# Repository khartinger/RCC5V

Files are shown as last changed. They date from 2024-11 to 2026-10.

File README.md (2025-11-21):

<table><tr><td></td><td>
Last modified: 2025-11-21 <br>   
<h1>Controlling model railroad components with DCC, MQTT and manually</h1>
<a href="LIESMICH.md">==> Deutsche Version</a>&nbsp; &nbsp; &nbsp; 
</td></tr></table>   

[Directly to the table of contents of this repository](#x20)   

# Introduction
Switching points is an important part of model railroading. There are many ways to control turnouts, uncouplers, disconnectable tracks and other components. Who doesn't want to be able to do this in different ways?    
The following image shows a part of an RCC control (RCC = Railway-Component-Control) with information display, switching and LED feedback.   
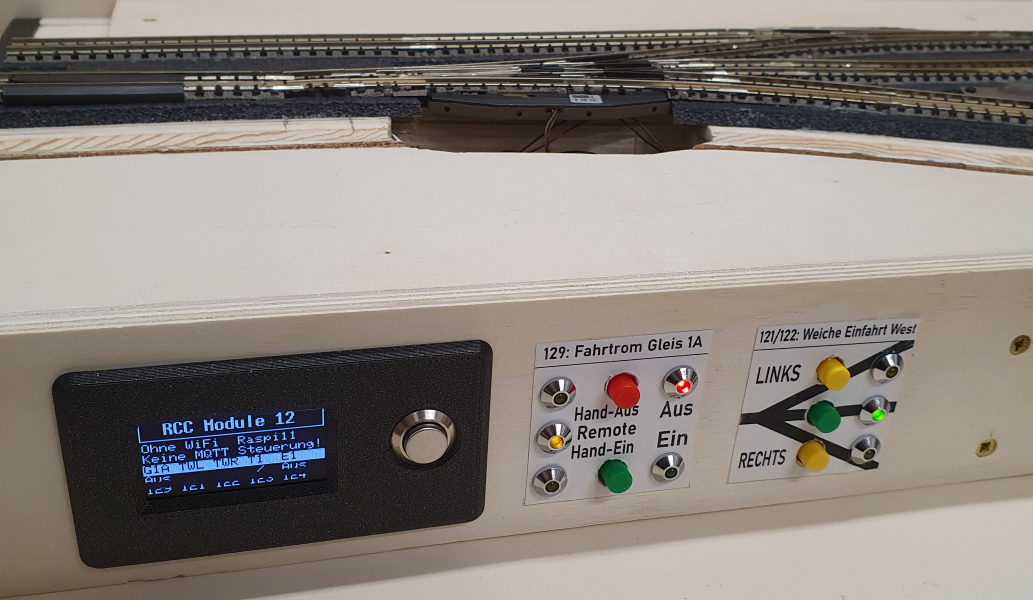
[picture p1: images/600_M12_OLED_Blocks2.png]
Example RCC controller
   
_Figure 1: Example user interface RCC control unit_   

## Traditional switching of turnouts etc.   
The simplest method of switching is, of course, to do it all by hand. In this case, you don't even need point machines. But with more distant or distributed components, this mode of operation quickly becomes cumbersome.   
For this reason, magnetic drives are usually used to switch the components. In the simplest case, the AC voltage is switched directly:   

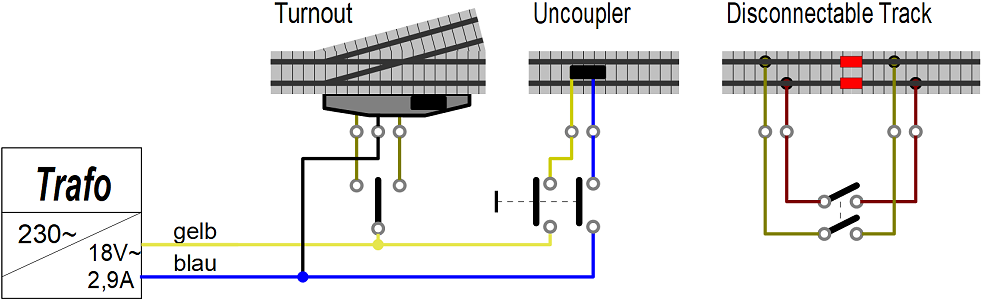
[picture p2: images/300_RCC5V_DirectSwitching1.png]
RCC5V_DirectSwitching
   
_Figure 2: Direct switching of model railway components   
(turnout = turnout, uncoupler = uncoupler track, disconnectable track = disconnectable track)_   

However, direct switching of the AC voltage has disadvantages: There is no feedback on the actual switching status and automatic switching of several components is not possible.   
These disadvantages can be eliminated by commercial, digital control systems. Unfortunately, this is usually associated with considerable costs. For this reason, self-construction is an option, which also offers additional possibilities and flexibility.   

## How to do it better?
If you like building things yourself, you've come to the right place. The low-cost RCC (Railway Component Control) model railroad component controller presented here allows you to switch model railroad components in three different ways:   
* directly on the module or on the layout at the touch of a button   
* via DCC   
* via MQTT commands &uuml;over the WLAN   

In the standard version, up to 32 digital outputs and inputs are available. This means that a maximum of 16 two-way switches or 10 three-way switches etc. can be controlled. This number is normally sufficient for modules.   
Expansion of the system is generally possible and only depends on the I²C-IO expanders used.   

Some skills are advantageous for the successful use of the RCC system:   
* Soldering and some manual dexterity   
* Compiling and uploading a file to an ESP32 microcontroller   
* Basic knowledge of the open source [circuit board layout program KiCad](https://www.kicad.org/)   
* Basic knowledge of MQTT, if MQTT is to be used for control   

# How do I get started?
1. you should first get an overview of the [contents of this repository](#x20) and [the RCC system](#x30). This is provided in the chapters below in this manual.   
2. If the RCC system is the right choice, the requirements for your own system have to be defined:   
* Which components are needed?
* How many of each type are needed?
* Which DCC address for which device?   
_Example demo program_:   
1x uncoupler with DCC address 11, 1x two-way turnout (DCC 21), 1x three-way turnout (DCC 31 and 32), 1x traction current (DCC 41) and 1x flashing light (DCC 51).   
3. the next step is to manufacture the required components. How to do this is described in the chapter [“How do I start the RCC project?” (/fab/rcc0_start/README.md)](/fab/rcc0_start/README.md).   
4. the demo program is then adapted to your own system and the ESP32 microcontroller is programmed. This is described in chapter [`/software/rcc_demo1
/CUSTOMIZE_E.md`](/software/rcc_demo1/CUSTOMIZE_E.md).   
5. Finally, all components are wired and the entire system is tested.   

The detailed description of the [construction of module #12: “passing loop and siding”](/examples/module12/LIESMICH.md) can also be a great help.   

[To the top of the page](#up)   

# Overview
This repository deals with the production and use of components for controlling turnouts, uncouplers, disconnectable tracks etc. on an electric model railroad using DCC, MQTT or manually.   
The following topics are covered in various subdirectories:   

__Information about the system__   
* [How do I begin the RCC project?](/fab/rcc0_start/README.md)   
* [Electrical connection of railroad modules according to NEM 908D](/info/con_NEM908/README.md)   
* [Drill holes and covers for the front of the module](/info/frontpanel/README.md)   

__Manufacturing the system components__   
* [Manufacturing of Components for the power supply](/fab/rcc1_supply/README.md)   
* [Manufacturing of the ESP32-Shields](/fab/rcc2_esp32/README.md)   
* [Manufacturing of i2c boards](/fab/rcc3_i2c/README.md)   
* [Manufacturing of the switching blocks](/fab/rcc4_block/README.md)   
* [Manufacturing of additional boards](/fab/rcc5_add_ons/README.md)   
* [KiCad files of RCC components](/fab/kicad/README.md)   

__Software for the ESP32__   
* [MQTT commands for controlling the components](/software/mqtt/README.md)   
* [Overview of the demo software](/software/rcc_demo1/README.md)   
* [Customize the demo software to your own needs](/software/rcc_demo1/CUSTOMIZE_E.md)   
* [Structure of the demo software in detail](/software/rcc_demo1/DETAILS_E.md)   
* [Automatic execution of MQTT command sequences](/software/mqtt/README.md#x30)   

__Examples, use of the system__   
* [Example wiring of a turnout](/examples/exampleTurnout2/README.md)   
* [Construction of the “RCC block tester”](/examples/blocktester/README.md)   
* [Construction of module 12: “passing loop and siding”](/examples/module12/README.md)   
* [Construction of module 13: “reverse loop - west”](/examples/module13/README.md)   
* [Construction of module 14: “Two tracks to one track”](/examples/module14/README.md)   
* [Conversion of module M01: “Track 1 to 2 with goods shed (2010)”](/examples/module01/README.md)   

__Other practical ideas for modules and the like__   
* [module dust cover](/info/dust_cover/README.md)   

[To the top of the page](#up)   

# The RCC-system at a glance   
The RCC system has a modular structure and mechanically consists of a series of modules or blocks. Logically, it consists of six parts:   

1. __FEED-IN__ (power supply): Generation and provision of the supply voltage (here AC voltage) and the DCC signals for the RCC system by external components.   
2. __SUPPLY__ (module supply): The AC voltage, the traction current and the DCC signal for switching the magnetic articles are taken from the 25-pin plug according to NEM908 and a separate 5V DC voltage is generated.   
3. __&micro;C__ (microcontroller): The microcontroller, equipped with additional shields, is used to control the module. An ESP32 is used, which also handles communication with the MQTT broker.  
4. __I2C__: Connection between the microcontroller and the control blocks (RCC blocks). I2C I/O expander boards with PCF8574 are used for this purpose.   
5. __RCC block__: The control element for _a_ model railroad component with local operating and display elements.   
6. the __model railroad components__ such as turnouts, uncouplers and disconnectable tracks.   

RCC5V_BlockDiagram1x   
_Figure 3: Block diagram for switching railroad components with 5V_   

By using the I2C-I/O-Expander-Boards it is possible to control several components:   
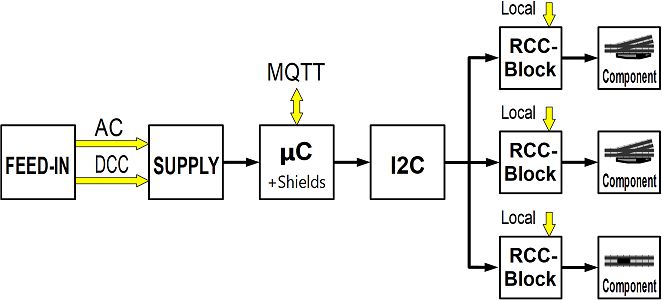
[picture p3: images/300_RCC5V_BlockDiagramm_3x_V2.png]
RCC5V_BlockDiagram3x
   
_Figure 4: Block diagram switching several railroad components with 5V_   

# Practical setup
Before e.g. the first switching of a turnout with RCC, some components must first be manufactured. How to do this is described in the chapter [“How do I start the RCC project?” (/fab/rcc0_start/README.md)](/fab/rcc0_start/README.md).   
The following figure shows an example of the modules required to control a three-way turnout:   
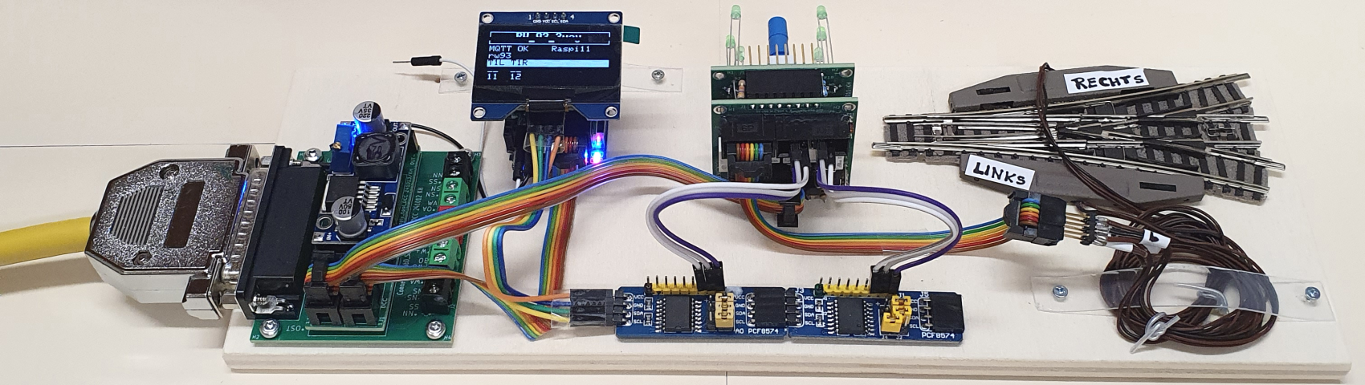
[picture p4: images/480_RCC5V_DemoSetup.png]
RCC5V_Demo_Setup
   
_Figure 5: Demo setup of an RCC-5V system: the individual parts_   

On the far left you can see the 25-pin connector with the 5V power supply (“SUPPLY”), behind it is the ESP32 with a 1.56 inch display (“&micro;C”). Two I2C-PCF8574 boards (“I2C”) are mounted in the front center, behind them the RCC block. On the right you can see a three-way turnout with two Fleischmann 640000 turnout drives. The electrical connection of the modules is made using 6-pin ribbon cables and wires.   

The following image shows an example of a possible front view of a module:   
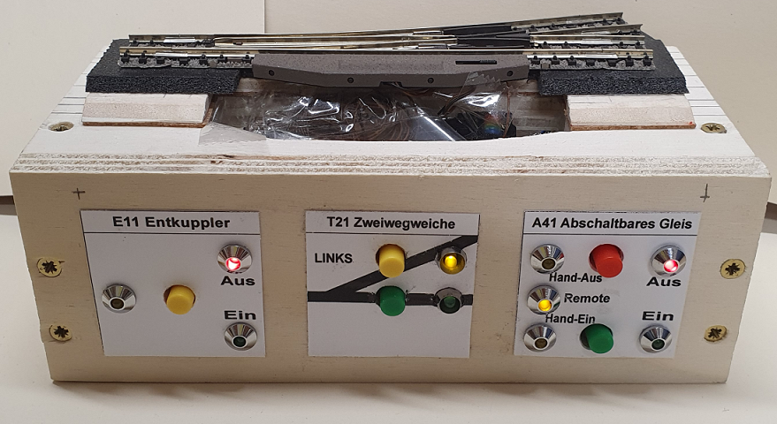
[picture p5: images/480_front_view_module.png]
Example front view
   
_Figure 6: Example of module front view (= operating side)_   

[To the top of the page](#up)

# Example: Circuit diagram for switching a turnout with the RCC5V system
The following picture shows the electrical circuit diagram for controlling a turnout with DCC, MQTT or manually. The light green rectangles represent circuit boards developed in KiCad 8.0 and manufactured by [PCB Way](https://www.pcbway.com/). To do this, simply install the PCB Way plug-in in KiCad and the data required for production is then transferred with a click of the mouse.   

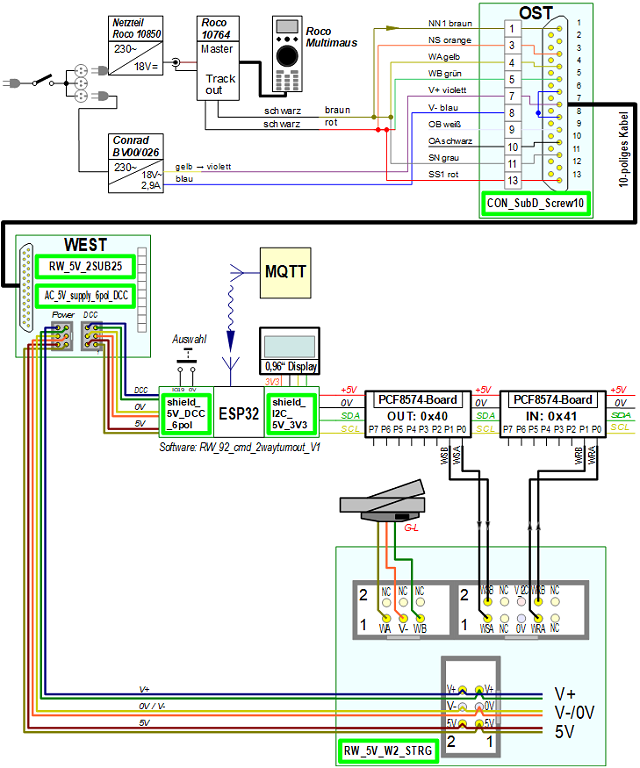
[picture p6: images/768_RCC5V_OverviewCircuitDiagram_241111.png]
overall_circuit_diagram overall circuit diagram
   
_Figure 7 Overall circuit diagram of the RCC-5V system_   

The upper third of the picture shows the supply of the DCC signal and the AC voltage (“FEED-IN”). The DCC signal for the traction current and the digital switching of the points is generated here with an old Roco-Multimaus, a 230V/18V/2.9A transformer [(e.g. BV00/026 from Conrad)](https://www.conrad.at/de/p/bv00-026-hochleistungstransformator-230-v-404288.html?refresh=true) is used for the AC voltage supply.   

The middle third of the picture shows the connection of the 25-pin connector to the microcontroller (5V and DCC signal) and to the RCC blocks (5V and AC signal). The ESP32 operates two separate I2C buses, one for the 1.56” OLED display (with 3.3V) and the second I2C bus for the PCF8574 boards (with 5V).   

Finally, the lower third of the picture shows the control of a two-way switch by an RCC block.   
The RCC block receives the switching command "Straight" (set WSA to 0V) or "Branch" (WSB=0V) from the microcontroller, switches the turnout and returns the state of the turnout (WRA=5V, WRB=0V for “Straight” or WRA=0V, WRB=5V for “Branch”). The RCC block also contains two buttons for local switching of the points and two LEDs for local display of the switching status of the points.   
You can also see that each RCC block requires a 5V and an AC voltage to switch the points.   

[To the top of the page](#up)

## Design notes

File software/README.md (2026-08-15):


<table><tr><td></td><td>
<h1>RCC – Software</h1><b><big>ESP32 Software for Controlling Model Railroad Components</big></b><br>  
Last updated: August 15, 2026    &nbsp; &nbsp; &nbsp; &nbsp;
<a href="#TableOfContents">→ Table of contents</a>&nbsp; &nbsp; &nbsp; &nbsp;
<a href="LIESMICH.md">→ Deutsche Version</a>
</td></tr></table>

# 1. What is this about?

This directory contains information about the **RCC software** and **ESP32 programs** for different hardware configurations.

## Contents

- [MQTT messages](https://github.com/khartinger/RCC5V/blob/main/software/mqtt/LIESMICH.md) – conventions for MQTT commands
- [Demo software Version 1](https://github.com/khartinger/RCC5V/tree/main/software/rcc_demo1) – everything in one file
- [Demo software Version 1a](https://github.com/khartinger/RCC5V/tree/main/software/rcc_demo1a) – split into several files
- [Demo software Version 2](https://github.com/khartinger/RCC5V/tree/main/software/rcc_demo2) – with additional control blocks

Further examples include **ESP32 programs for various railway modules**.

---   
[To the top of the page](#up)

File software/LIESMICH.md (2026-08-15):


<table><tr><td></td><td>
<h1>RCC – Software</h1><b><big>ESP32-Software zur Steuerung von Modellbahn-Komponenten</big></b><br>  
Stand: 15.8.2026    &nbsp; &nbsp; &nbsp; &nbsp;
<a href="#TableOfContents">→ Inhaltsverzeichnis</a>&nbsp; &nbsp; &nbsp; &nbsp;
<a href="README.md">→ English version</a>
</td></tr></table>

# 1. Worum geht es?

Dieses Verzeichnis enthält Informationen zur **RCC-Software** sowie **ESP32-Programme** für verschiedene Hardware-Konfigurationen.

## Inhaltsübersicht

- [MQTT-Nachrichten](https://github.com/khartinger/RCC5V/blob/main/software/mqtt/LIESMICH.md) – Vereinbarungen für MQTT-Befehle
- [Demo-Software Version 1](https://github.com/khartinger/RCC5V/tree/main/software/rcc_demo1) – alles in einer Datei
- [Demo-Software Version 1a](https://github.com/khartinger/RCC5V/tree/main/software/rcc_demo1a) – auf mehrere Dateien aufgeteilt
- [Demo-Software Version 2](https://github.com/khartinger/RCC5V/tree/main/software/rcc_demo2) – mit weiteren Steuerblöcken

Weitere Beispiele sind **ESP32-Programme für verschiedene Eisenbahnmodule**.

---   
[Zum Seitenanfang](#up)

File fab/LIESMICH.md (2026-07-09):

<table><tr><td></td><td>
Letzte &Auml;nderung: 7.7.2026 <br>   
<h1>Bauanleitungen für Module, Platinen und 3D-Teile</h1><h3></h3>
<a href="#TableOfContents">==> Inhaltsverzeichnis</a>&nbsp; &nbsp; &nbsp;  &nbsp; 
<a href="README.md">==> English version</a>
</td></tr></table>   

# Worum geht es?
Das Verzeichnis `fab` (f&uuml;r "_fabrication_") ist das "Fertigungszentrum" des RCC-Systems (RCC = Railway Component Control). Es enth&auml;lt Herstellungsdaten, Bauanleitungen, Zeichnungen und Beschreibungen von Teilen, die f&uuml;r das RCC-System ben&ouml;tigt werden. Die Daten sind auf folgende Unterverzeichnisse aufgeteilt:   

* [1. 3d](#x10)   
* [2. kicad](#x20)   
* [3. odg](#x30)   
* [4. rcc0_start](#x40)   
* [5. rcc1_supply](#x50)   
* [6. rcc2_esp3](#x60)   
* [7. rcc3_i2c](#x70)   
* [8. rcc4_block](#x80)   
* [9. rcc5_add_ons](#x90)   
* [10. rcc6_additional_components](#x100)   

Der folgende Text beschreibt den Inhalt der Verzeichnisse und enth&auml;lt Links zu den entsprechenden Anleitungen.   

# 1. 3d
Dieses Verzeichnis enth&auml;lt 3mf-Dateien f&uuml;r mechanische Bauteile, die mit einem 3D-Drucker hergestellt werden k&ouml;nnen. Beispiele sind   

* [Modulseite (Ost, West)](/fab/3d/LIESMICH.md#x10)   
* [Querverstrebung](/fab/3d/LIESMICH.md#x20)   
* [Sub-D-Stecker-Halterung](/fab/3d/LIESMICH.md#x30)   
* [OLED- und Taster-Einsatz](/fab/3d/LIESMICH.md#x40)   
* [Biegelehre f&uuml;r LEDs](/fab/3d/LIESMICH.md#x50)   
* [Weichenabdeckung f&uuml;r Zweiwegweiche](/fab/3d/LIESMICH.md#x60)   
* [Flache Weichenabdeckung f&uuml;r Zweiwegweiche](/fab/3d/LIESMICH.md#x70)   
* [Weichenabdeckung f&uuml;r Dreiwegweiche](/fab/3d/LIESMICH.md#x80)   

# 2. kicad
Dieses Verzeichnis enth&auml;lt die Kicad-Projekte aller Leiterplatten mit Schaltung und Platinenlayout. Mit dem Open Source [Layoutprogramm KiCad](https://www.kicad.org/) und zB dem Plug-in "PCBWay" kann man die dazugeh&ouml;rigen Leiterplatten bei einem Leiterplattenhersteller fertigen lassen.   

# 3. odg
Dieses Verzeichnis enth&auml;lt odg-Zeichnungen f&uuml;r allgemein g&uuml;ltige Informationen. Spezielle Zeichnungen, wie zum Beispiel die Cover der Beispiele und Module, sind bei den jeweiligen Projekten abgelegt.   
Die Bildschirm-Kopien von odg-Zeichnungen sind als png-Dateien abgespeichert und werden in den Markdown (.md)-Dokumenten angezeigt.   

[Zum Seitenanfang](#up)   

# 4. rcc0_start
Dieses Verzeichnis beschreibt die Dinge, die man ben&ouml;tigt, wenn man sich f&uuml;r den Selbstbau des RCC-Systems entschlossen hat:   
* [Welche Leiterplatten ben&ouml;tige ich und wie erstelle ich sie?](/fab/rcc0_start/LIESMICH.md#x20)   
* [Welche Bauteile ben&ouml;tige ich? (Grundausstattung an Bauteilen) ](/fab/rcc0_start/LIESMICH.md#x30)   
* [Welche Zukaufteile ben&ouml;tige ich?](/fab/rcc0_start/LIESMICH.md#x34)   
* [Welches Werkzeug ben&ouml;tige ich?](/fab/rcc0_start/LIESMICH.md#x36)   

Die Herstellung der RCC-Komponenten wird dann in den anderen Unterverzeichnissen dieses Verzeichnisses beschrieben.   

[Zum Seitenanfang](#up)   

# 5. rcc1_supply
In diesem Verzeichnis wird beschrieben, wie die Bl&ouml;cke zur Energieversorgung der Eisenbahnmodule nach NEM 908 gebaut werden. Dabei werden die Eigenschaften sowie die Best&uuml;ckung der Platinen erl&auml;utert, wie zum Beispiel   
* [Netzteil-Tr&auml;gerplatine (`AC_5V_6pol_DCC`)](/fab/rcc1_supply/LIESMICH.md#x22)   
* [Platine mit zwei 25-poligen Sub-D-Steckern und Netzteil (`RW_5V_2SUB25`)](/fab/rcc1_supply/LIESMICH.md#x32)   
* [Platine mit 25-poligem Sub-D-Stecker, Schraubklemmen und Netzteil (`RW_5V_SUB25_10`)](/fab/rcc1_supply/LIESMICH.md#x33)    
* [Platine mit 25-poligem Sub-D-Stecker und Schraubklemmen (`CON_SubD_Screw10`)](/fab/rcc1_supply/LIESMICH.md#x34)   

[Zum Seitenanfang](#up)   

# 6. rcc2_esp32
Die Steuerung des RCC-Systems (Railway Component Control) erfolgt mit einem "ESP32 D1 Mini" Multiprozessor und Zusatzplatinen. Die Zusatzplatinen dienen dazu, das DCC-Signal und den Taster einzulesen sowie die I²C-Busse f&uuml;r das Display und die PCF85745-Ein-Ausgabe-Expander bereitzustellen.   
In diesem Verzeichnis werden die Herstellung bzw. Best&uuml;ckung folgender Platinen beschrieben:   
* [ESP32-Shield I²C-Bus (Shield_I2C_5V_3V3)](/fab/rcc2_esp32/LIESMICH.md#x20)   
* [ESP32-Shield mit 5V-Versorgung, Taster und DCC (Shield_5V_DCC_6pol)](/fab/rcc2_esp32/LIESMICH.md#x30)   
* [das erweiterte I²C-Board `Shield_I2C_5V_3V3_big`](/fab/rcc2_esp32/LIESMICH.md#x40)   

[Zum Seitenanfang](#up)   

# 7. rcc3_i2c
In diesem Verzeichnis werden die I²C-Komponenten des Systems beschrieben, wie ZB   * [I²C-PCF8574-I/O-Platinen](/fab/rcc3_i2c/LIESMICH.md#x10)   
* [I²C-Halterung 20 mm](/fab/rcc3_i2c/LIESMICH.md#x20)   
* [I2C-LED-Platine](/fab/rcc3_i2c/LIESMICH.md#x40)   
* [I²C-Platine mit Pull-up-Widerst&auml;nden](/fab/rcc3_i2c/LIESMICH.md#x60)   

[Zum Seitenanfang](#up)   

# 8. rcc4_block
Auf dieser Seite wird - nach einigen allgemeinen Hinweisen zu Bl&ouml;cken - das Herstellen folgender Bl&ouml;cke beschrieben:   
* [Block Zweiwegweiche (W2)](/fab/rcc4_block/LIESMICH.md#x20)   
* [Block Dreiwegweiche (W3)](/fab/rcc4_block/LIESMICH.md#x30)   
* [Block Entkuppler (1OUT)](/fab/rcc4_block/LIESMICH.md#x40)   
* [Block Abschaltbares Gleis (2IO)](/fab/rcc4_block/LIESMICH.md#x50)   
* [Block Zweifachumschalter (DPDT)](/fab/rcc4_block/LIESMICH.md#x60)   

[Zum Seitenanfang](#up)   

# 9. rcc5_add_ons
In diesem Verzeichnis wird die Herstellung von RCC-Erg&auml;nzungsplatinen beschrieben.   
Diese Platinen sind f&uuml;r den Betrieb des RCC-Systems nicht unbedingt notwendig, allerdings vereinfachen sie die Verkabelung.   
__*Beispiel*__:   
Die I²C-Leitungen für die I²C-PCF8574-I/O-Platinen kann man entweder   
* einzeln am 10-poligen Wannenstecker J4 eines Blocks anstecken oder   
* am Erg&auml;nzungsboard `CON_10pol_PIN` anstecken und dann gemeinsam am 10-poligen Wannenstecker J4 eines Blocks anschließen.   

Unter anderem werden folgende Erg&auml;nzungsplatinen beschrieben:   
* [Halterung f&uuml;r Schaltbl&ouml;cke (RW_LEER_LED)](/fab/rcc5_add_ons/LIESMICH.md#x20)   
* [Fahrstromverteiler (CON_2pol_141)](/fab/rcc5_add_ons/LIESMICH.md#x30)   
* [Verteilerplatine von 6-poligem Kabel auf 3 Schraubklemmen (CON_6pol_3)](/fab/rcc5_add_ons/LIESMICH.md#x40)   
* [Verteilerplatine von 6-poligem Kabel auf 6 Schraubklemmen (CON_6pol_6)](/fab/rcc5_add_ons/LIESMICH.md#x50)   
* [Fahrstromschalter einfach (CON_1xIO)](/fab/rcc5_add_ons/LIESMICH.md#x60)   
* [Fahrstromschalter zweifach (CON_2xIO)](/fab/rcc5_add_ons/LIESMICH.md#x70)   
* [Verteilerplatine von 10-poligem Kabel auf Pins (CON_10pol_2x4)](/fab/rcc5_add_ons/LIESMICH.md#x80)   

[Zum Seitenanfang](#up)   

# 10. rcc6_additional_components
Dieses Verzeichnis enthält zusätzliche, ergänzende Komponenten für ein RCC-System, wie Pulserkennung oder Fahrstromerkennung.   

[Zum Seitenanfang](#up)

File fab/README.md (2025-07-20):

<table><tr><td></td><td>

Last modified: 2025-07-20 <br>   
<h1>Assembly instructions for modules, circuit boards and 3D parts</h1>
<a href="LIESMICH.md">==> Deutsche Version</a>&nbsp; &nbsp; &nbsp; 
</td></tr></table>   

<a href="LIESMICH.md"><b> Sorry! This page is currently only available in German.</b></a>   

[To the top of the page](#up)

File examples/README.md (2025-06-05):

<table><tr><td></td><td>
Last modified: 2025-06-05 <br>   
<h1>RCC Example Applications</h1>
<a href="LIESMICH.md">==> Deutsche Version</a>&nbsp; &nbsp; &nbsp; 
</td></tr></table>    

This directory contains the following examples:   

* [__`blocktester`__: Construction of the “RCC block tester”](/examples/blocktester/README.md)   
* [__`exampleTurnout2`__: Example wiring of a turnout](/examples/exampleTurnout2/README.md)   
* [__`module01`__: Conversion of module M01: “Track 1 to 2 with goods shed (2010)”](/examples/module01/README.md)   
* [__`module12`__: Construction of module 12 “passing loop and siding”](/examples/module12/README.md)   
* [__`module13`__: Construction of module 13 “reverse loop - west”](/examples/module13/README.md)   
* [__`module14`__: Construction of module 14: “Two tracks to one track”](/examples/module14/README.md)   

[To the top of the page](#up)

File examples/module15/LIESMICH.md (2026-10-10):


<table><tr><td></td><td>
<h1>Modul 15: Minimodul P20-Sub-D-Einspeisung</h1><b><big>Modul mit Einspeisung über Flachbandkabel oder Sub-D-Stecker</big></b><br>  
Stand: 10.10.2026    &nbsp; &nbsp; &nbsp; &nbsp;
<a href="#TableOfContents">→ Inhaltsverzeichnis</a>&nbsp; &nbsp; &nbsp; &nbsp;
<a href="README.md">→ English version</a>
</td></tr></table>

# Worum geht es?
**Modul 15** ist ein gerades, nur **25 cm × 25 cm** großes Modul ohne Elektronik und Schaltblöcke. Es ermöglicht die Einspeisung des Fahrstroms sowohl über den 25-poligen Sub-D-Stecker als auch über den 20-poligen Flachbandstecker **„P20“**.  

Modul M15   
_Bild: Rahmen mit Grundplatte und Gleisen._   

##  Inhalt
1. [Vorbereitung und Einkauf](#x10)  
2. [Rahmenbau](#x20)  
3. [Gleisbau](#x30)  
4. [Elektrik](#x40)  

## Eigenschaften des Moduls
| | | 
|---|---|
| Modulgröße | 25 x 25 cm² | 
| Gleismaterial  | Fleischmann Spur-N-Gleis mit und ohne Schotterbett | 
| Gleisbild | 1x Ausgleichsgleis, 2x 55,5 mm, 1x 45,5 mm | 
| Elektrischer Anschluss | * 2x 25-poliger SUB-D-Stecker (entsprechend NEM 908D, je 1x WEST und OST) <br>* 2x 20-poliger Wannenstecker (auf der Rückseite) | 
| Fahrstrom | Analog- oder DCC-Betrieb | 
| Steuerung der Schaltkomponenten | - | 
| Bedienelemente mit R&uuml;ckmeldung | - | 
| WLAN | - | 
| MQTT: IP-Adresse des Brokers (Host) | - | 
| Sonstiges | * Einfaches Verbinden mit anderen Modulen durch ein ausziehbares Gleis am Segment-Ende | 

# 1. Vorbereitung und Einkauf

## 1.1 Schienenkauf
### 1.1.1 Entwurf des Gleisplans

Auf der Westseite befindet sich ein ausziehbares Gleis, das das Verbinden mit anderen Modulen erleichtert.  
Da die Modullänge von 25 cm nicht mit den Standardgleislängen von Fleischmann erreicht werden kann, muss ein gerades Gleis (z. B. 9103) auf **45,5 mm** gekürzt werden.  
Der folgende Gleisplan wurde mit [AnyRail](https://www.anyrail.com/) erstellt.  

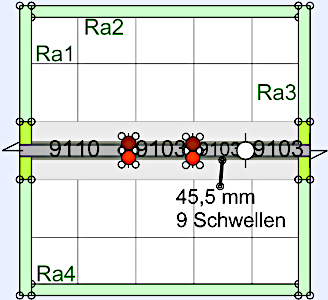
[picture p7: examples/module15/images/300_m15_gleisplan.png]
M15 Gleisplan
  
_Bild: Gleisplan Modul 15_  

Die braunen und roten Kreise markieren die Fahrstromeinspeisungen.  

### 1.1.2 Schienenkauf - St&uuml;ckliste
Zum Bau des Moduls werden folgende Gleise und Zubeh&ouml;r ben&ouml;tigt:   
| Anzahl | Nummer | Name | Euro/Stk | Euro | 
| :---: | :---: | :--- |  ---: |  ---: |
| 1 | 9110 | Ausgleichsgleis gerade 83mm-111mm | 14,60 | 14,60 | 
| 3 | 9103 | Gerade 55, 5 mm | 4,40 | 13,20 | 

Gesamtkosten 2025: ca. 27,80 Euro   

## 1.2 Rahmen
### 1.2.1 Modulrahmen
Der 25 x 25 cm² gro&szlig;e Modulrahmen ist 6 cm hoch und besteht aus zwei Seitenteilen ("Ost" und "West") und zwei L&auml;ngsteilen ("Nord" und "S&uuml;d") ohne Querstreben. Die Gel&auml;ndeplatte wird in den Rahmen eingelegt.   
Die Teile des Rahmens k&ouml;nnen entweder aus Holz hergestellt oder mit dem 3D-Drucker gedruckt werden. Auch eine gemischte Bauweise ist m&ouml;glich, zB Seitenteile 3D-Drucken, L&auml;ngsteile aus Holz.   

### 1.2.2 Holz-Rahmen

#### Pappelsperrholz 10 mm
| St&uuml;ck | Abmessung | Kurzbezeichnung | Verwendung | 
|:-----:|:---:|:---:|:---|
| 1 | 230 x 230 mm² | - | Gel&auml;nde-Grundplatte | 
| 2 | 230 x 60 mm²  | Ra2, Ra4 | Rahmen au&szlig;en Nord, S&uuml;d | 
| 2 | 250 x 70 mm²  | Ra1, Ra3 | Rahmen au&szlig;en West, Ost | 

#### Pappelsperrholz 5 mm (oder 4 mm)
| St&uuml;ck | Abmessung | Anmerkung | 
|:-----:|:---:|:---|
| 1 | 50 x 250 mm² | Bahndamm  | 

#### Holzrahmen: Kleinteile
4x Pappelsperrholz 10 mm stark, 70 x 35 mm² f&uuml;r die Halterungen der Sub-D-Stecker.   
4x kleine Holzst&uuml;cken 10 x 10 x 50 mm³ als zus&auml;tzliche Auflager f&uuml;r die Grundplatte. 

#### Holzrahmen: Verbrauchsmaterial
| St&uuml;ck | Nummer | Lieferant  | Bezeichnung | 
|:---:|:---:|:---|:---|
| 1 | | Ponal | Holzleim Express | 
| 1 | 4002364114016 | Albrecht | Yacht- und Bootslack, farblos, hochgl&auml;nzend | 
| 1 | | | Topfreiniger (Abwasch-Schwamm) | 
| 2 | | | Paar Einmal-Handschuhe | 
| 1 | | | Schleifpapier K&ouml;rnung 240 | 

### 1.2.3 3D-Rahmen
* 2x Seitenteile: [`Rahmen_SeiteEingleisig_260906.FCStd`](https://github.com/khartinger/RCC5V/blob/main/fab/3d/Rahmen_SeiteEingleisig_260906.FCStd)  
* 1x Längsteil Nord: [`Rahmen_Back_N__2xP20_230mm_261008.FCStd`](https://github.com/khartinger/RCC5V/blob/main/fab/3d/Rahmen_Back_N__2xP20_230mm_261008.FCStd)  
* 1x Längsteil Süd: [`Rahmen_Back_S__230mm_261008.FCStd`](https://github.com/khartinger/RCC5V/blob/main/fab/3d/Rahmen_Back_S__230mm_261008.FCStd)  
* Gelände-Grundplatte: Pappelsperrholz 10 mm, 230 x 230 mm²

### 1.2.4 Kleinteile
8x Schraube M3 x 30 mm Senkkopf, Kreuzschlitz, selbstschneidend []()  (zB Fa. Spax 4 003530 021251)   

## 1.3 Elektrische Komponenten
### 1.3.1 P20-Anschluss in Nord
Als Anschluss für eine 20-polige Flachbandkabel-Buchse ("P20") wird das Board PCB_F_CON_20_3x_Screw10` verwendet.  

rcc7_CON_20_3x_Screw10_V1_assembled rcc7_CON_20_Screw10_V1_assembled   

Der Bau ist [hier](https://github.com/khartinger/RCC5V/blob/main/fab/rcc7_p20/LIESMICH.md#x22) beschrieben.  

### 1.3.2 P20-Sub-D-Umsetzer
Zum Umsetzen von P20 auf Sub-D-Stecker wird das Board `PCB_F_CON_20_2x_2xSubD` verwendet.  

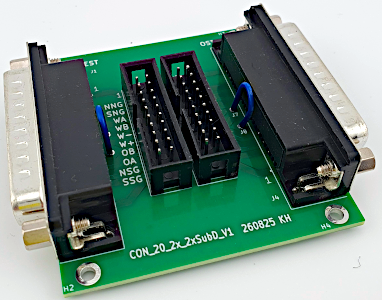
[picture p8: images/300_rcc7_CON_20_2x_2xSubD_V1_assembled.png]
rcc7_CON_20_2x_2xSubD_V1_assembled
   

Der Bau ist [hier](https://github.com/khartinger/RCC5V/blob/main/fab/rcc7_p20/LIESMICH.md#x12) beschrieben.  

# 2. Rahmenbau

## 2.1 Einleitung
Jedes Modul besteht aus einem Rahmen mit Querverbindungen und der Grundplatte, die die Gleise und Landschaft tr&auml;gt. Zuerst erstellt man den Modul-Rahmen. Das hat zwei Vorteile:   
1. Der Test, ob die Grundplatte in den Rahmen passt, kann mit der leeren Grundplatte erfolgen. Falls die Grundplatte zu gro&szlig; ist, kann sie einfach zugeschnitten oder zugeschliffen werden.   
2. Beim Aufkleben der Gleise auf die Grundplatte sind an den Modul&uuml;berg&auml;ngen (Ost und West) bereits die Seitenteile mit den Gleisausnehmungen vorhanden. So sind die Gleise beim Aufkleben sicher an der richtigen Position.   

Der Rahmen des Moduls 15 besteht aus vier Teilen:  
* 2x Seitenteil [`Rahmen_SeiteEingleisig_260906`](/fab/3d/Rahmen_SeiteEingleisig_260906.FCStd)  
* 1x Leerer Vorderteil [`Rahmen_Front_S__230mm_260408`](/fab/3d/Rahmen_Front_S__230mm_261008.FCStd)  
* 1x Rückteil [`Rahmen_Back_N__2xP20_230mm_261008`](/fab/3d/Rahmen_Back_N__2xP20_230mm_261008.FCStd)  

## 2.2 Seitenteile `Rahmen_SeiteEingleisig_260906`  
Die Seitenteile sind an eine (ehemalige?) Norm von n-spur.at angelehnt, wobei das Bahnk&ouml;rper-Profil aber der NEM122 entspricht:   

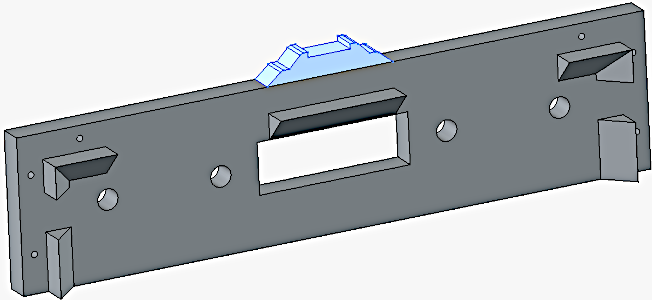
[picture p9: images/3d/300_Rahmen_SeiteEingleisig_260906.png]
Modul Seitenteil eingleisig
  

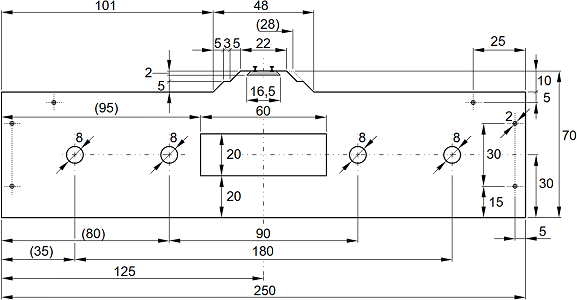
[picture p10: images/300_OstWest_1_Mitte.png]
Modul_OstWest_1_Mitte
   
_Bild: Ma&szlig;e f&uuml;r die Seitenteile Ost und West (Modulbreite 250mm, ein in der Mitte liegendes Gleis)._   

* Die vier 8mm-Bohrungen dienen zum Verbinden der Module mit 8 mm-Fl&uuml;gelschrauben und Fl&uuml;gelmuttern.   
* Die linken und rechten vier 2 mm-Bohrungen dienen zum Anschrauben der Nord- und S&uuml;dwand.   
* Die oberen zwei 2mm-Bohrungen dienen zum Fixieren der Gel&auml;nde-Grundplatte (falls erforderlich).   
* Die 60x20 mm²-Ausnehmung dient zum Durchf&uuml;hren des 25-poligen Sub-D-Steckers.   

## 2.3 Leerer Vorderteil `Rahmen_Front_S__230mm_260408`  

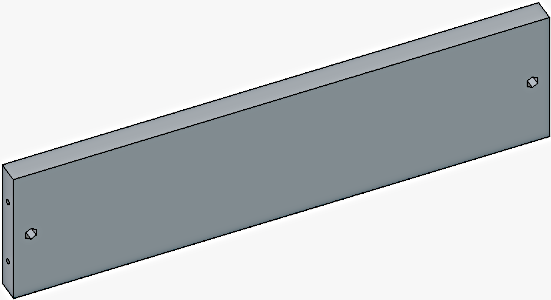
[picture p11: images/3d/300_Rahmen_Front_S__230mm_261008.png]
Rahmen_Front_S__230mm_261008
   

Die beiden Sechskant-Ausnehmungen dienen zur Befestigung einer Plexiglasabdeckung.  

## 2.4 Nordteil `Rahmen_Back_N__2xP20_230mm_261008`

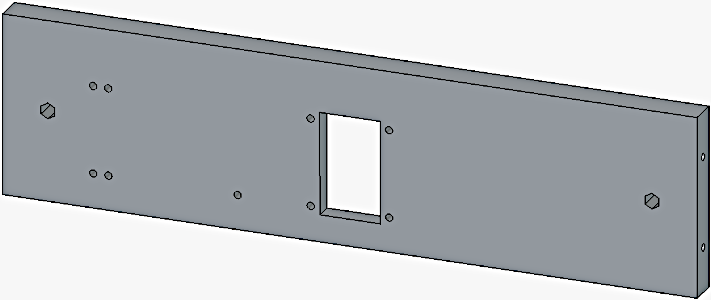
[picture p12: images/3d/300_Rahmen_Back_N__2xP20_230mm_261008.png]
Rahmen_Back_N__2xP20_230mm_261008
   

Größe der Ausnehmung für die P20-Stecker:  
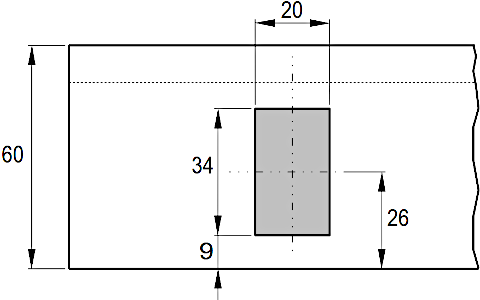
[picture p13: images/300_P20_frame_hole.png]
P20 Ausnehmung
   

## 2.5 Zusammenbau des Rahmens
1. Anordnen der 3D-Teile im Quadrat.  
2. Gelände-Grundplatte auf die Rahmenteile legen.  
3. Zusammenschrauben des Rahmens mit 8 Schrauben M3 x 30 mm (Senkkopf, Kreuzschlitz, selbstschneidend).  

# ..ToDo.. ..ToDo.. ..ToDo..

# 3. Gleisbau

# 4. Elektrik

[Zum Seitenanfang](#up)

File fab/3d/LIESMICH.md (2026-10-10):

<table><tr><td></td><td>
Letzte &Auml;nderung: 31.3.2025 <br>   
<h1>3D Daten</h1>
<a href="README.md">==> English version</a>&nbsp; &nbsp; &nbsp; 
</td></tr></table>   

# Einleitung
Dieses Verzeichnis enth&auml;lt FreeCad- und 3mf-Dateien f&uuml;r verschiedene Bauteile von Eisenbahnmodulen.   
Die 3mf-Dateien befinden sich im Unterverzeichnis `3mf`.

# Modulseite eingleisig (Ost, West)
__Fusion-Datei__:  ModulSeite_250209.3mf   
__Freecad-Datei__: [Rahmen_SeiteEingleisig_260906.FCStd](/fab/3d/Rahmen_SeiteEingleisig_260906.FCStd)   
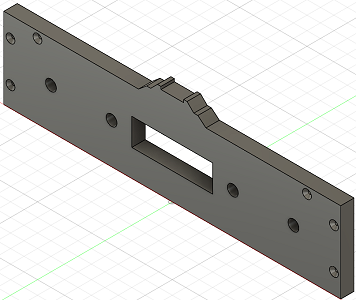
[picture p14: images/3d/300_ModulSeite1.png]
Modul Seitenteil
 Modul Seitenteil eingleisig   
_Bild 1: Seitenteil (Ost, West) eines 25 cm breiten Moduls mit einem Gleis in der Mitte_   

# Modulseite zweigleisig (Ost, West)
__Freecad-Datei__: [Rahmen_SeiteZweigleisig_260906.FCStd](/fab/3d/Rahmen_SeiteZweigleisig_260906.FCStd)   
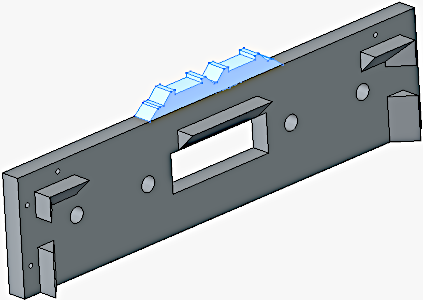
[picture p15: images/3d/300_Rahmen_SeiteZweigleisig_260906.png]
Modul Seitenteil zweigleisig
   
_Bild 2: Seitenteil (Ost, West) eines 25 cm breiten Moduls mit zwei Gleisen in der Mitte_   

# Querverstrebung
__Fusion-Datei__: Querverstrebung_250209.3mf   
__Freecad-Datei__: [Querverstrebung_23cm.FCStd](/fab/3d/Querverstrebung_23cm.FCStd)   
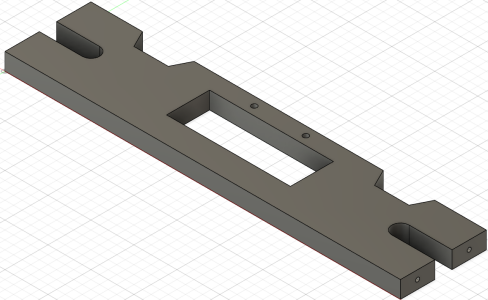
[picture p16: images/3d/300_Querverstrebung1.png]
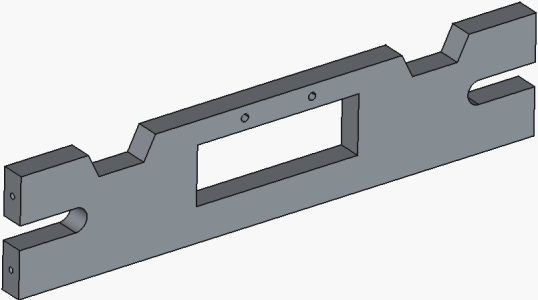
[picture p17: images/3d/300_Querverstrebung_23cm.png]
     
_Bild 3: Querverstebung in einem 25 cm breiten Modul_   

# Sub-D-Stecker-Halterung
Die Halterung f&uuml;r den Sub-D-Stecker besteht aus zwei U-f&ouml;rmigen Teilen.   
__Fusion-Datei__: Bracket_sub-D_250209.3mf   
__Freecad-Datei__: [Bracket_sub-D.FCStd](/fab/3d/Bracket_sub-D.FCStd)   
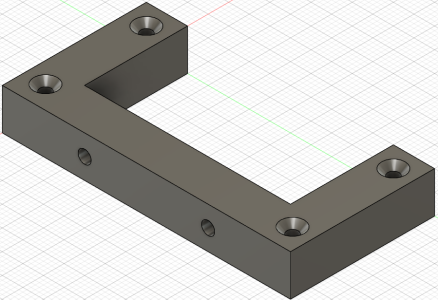
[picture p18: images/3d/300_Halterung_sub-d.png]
Halterung Sub-D-Stecker
 
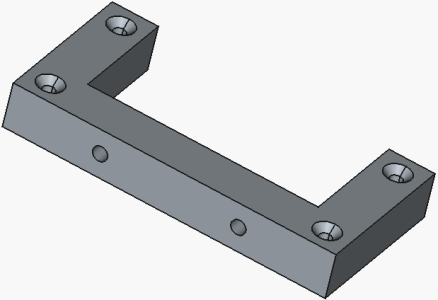
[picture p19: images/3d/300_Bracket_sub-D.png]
   
_Bild 4: Halterung f&uuml;r Sub-D-Stecker_   

# OLED- und Taster-Einsatz
__Fusion-Datei__: OLED-Mount_250209.3mf   
__Freecad-Datei__: [OLED_Mount.FCStd](/fab/3d/OLED_Mount.FCStd)   
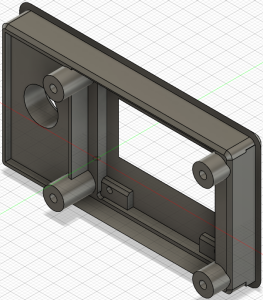
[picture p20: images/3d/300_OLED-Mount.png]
OLED- und Taster-Einsatz
 
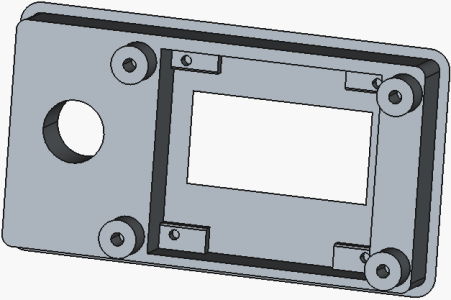
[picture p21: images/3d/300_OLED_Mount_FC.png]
OLED- und Taster-Einsatz
   
_Bild 5: Halterung f&uuml;r die OLED-Anzeige und den Taster_   

# Biegelehre f&uuml;r LEDs
__Fusion-Datei__: Biegelehre_LED_v4.3mf   
__Freecad-Datei__: [Biegelehre_LED.FCStd](/fab/3d/Biegelehre_LED.FCStd)   
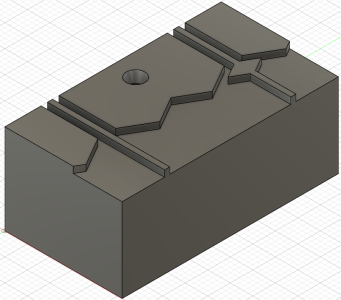
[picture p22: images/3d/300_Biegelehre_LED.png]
Biegelehre f&uuml;r LEDs
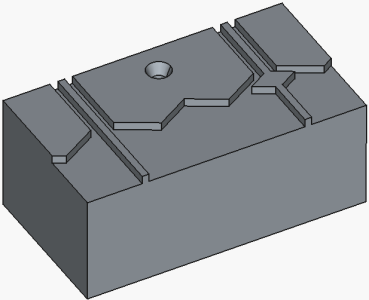
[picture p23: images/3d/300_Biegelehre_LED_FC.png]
Biegelehre f&uuml;r LEDs
     
_Bild 6: Biegelehre f&uuml;r LEDs_   

# Weichenabdeckung f&uuml;r Zweiwegweiche
__Datei__: Weichenabdeckung_2Weg_1_v4.3mf   
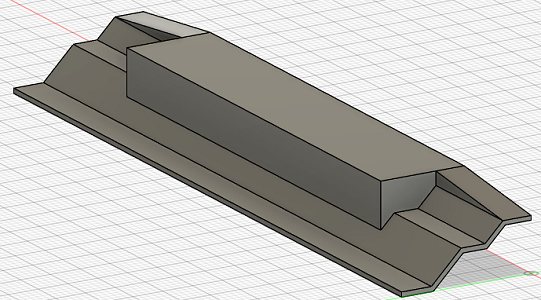
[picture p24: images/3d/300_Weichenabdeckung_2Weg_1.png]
Weichenabdeckung f&uuml;r Zweiwegweiche
   
_Bild 7: Weichenabdeckung f&uuml;r Zweiwegweiche_   

# Flache Weichenabdeckung f&uuml;r Zweiwegweiche
__Datei__: Weichenabdeckung_2Weg_flach v1.3mf   
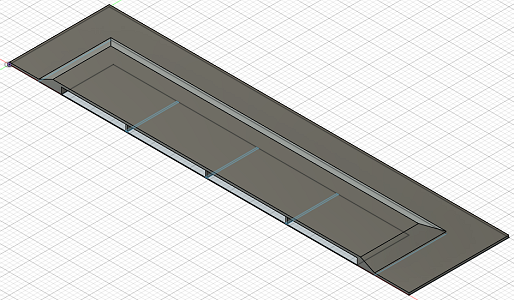
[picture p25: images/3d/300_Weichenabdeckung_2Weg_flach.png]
Flache Weichenabdeckung f&uuml;r Zweiwegweiche
   
_Bild 8: Flache Weichenabdeckung f&uuml;r Zweiwegweiche_   

# Weichenabdeckung f&uuml;r Dreiwegweiche
__Datei__: Weichenabdeckung_3Weg_beide_v2.3mf   
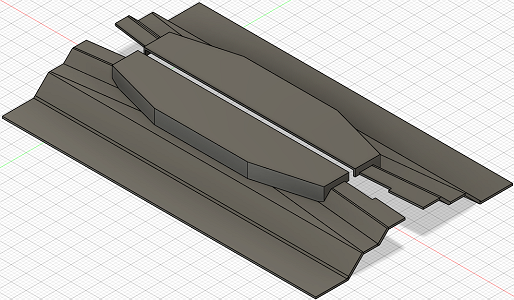
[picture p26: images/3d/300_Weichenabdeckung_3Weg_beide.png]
Weichenabdeckung f&uuml;r Dreiwegweiche
   
_Bild 9: Weichenabdeckung f&uuml;r Dreiwegweiche_   

# Hilfswerkzeug Stütze eingleisig
Möchte man ein Modul auf der Unterseite bearbeiten (um zB die Elektronik zu verdrahten), so muss man das Modul mit den Schienen oder der Landschaft auf den Tisch legen. Um dies zu vermeiden, werden links und rechts (also "Ost" und "West") Stützen montiert, auf denen das Modul dann ruht.   

__Freecad-Datei__: [ModulStützeEingleisig_251109.FCStd](/fab/3d/ModulStützeEingleisig_251109.FCStd)   
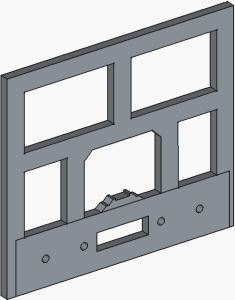
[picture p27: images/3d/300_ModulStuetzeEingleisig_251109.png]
Hilfswerkzeug Stütze eingleisig
   
_Bild 10: Hilfswerkzeug eingleisige Stütze_   

# Hilfswerkzeug Stütze zweigleisig
Möchte man ein Modul auf der Unterseite bearbeiten (um zB die Elektronik zu verdrahten), so muss man das Modul mit den Schienen oder der Landschaft auf den Tisch legen. Um dies zu vermeiden, werden links und rechts (also "Ost" und "West") Stützen montiert, auf denen das Modul dann ruht.   

__Freecad-Datei__: [ModulStützeZweigleisig_251109.FCStd](/fab/3d/ModulStützeZweigleisig_251109.FCStd)   
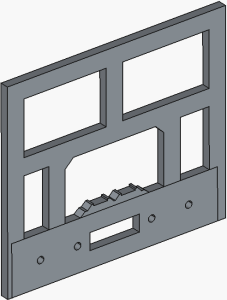
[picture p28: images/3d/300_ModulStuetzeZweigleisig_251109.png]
Hilfswerkzeug Stütze zweigleisig
   
_Bild 11: Hilfswerkzeug zweigleisige Stütze_   

# Hilfswerkzeug Klammer 265 mm
__Freecad-Datei__: [Klammer265.FCStd](/fab/3d/Klammer265.FCStd)   
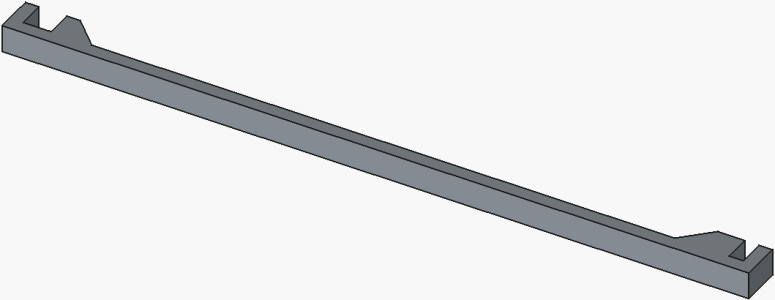
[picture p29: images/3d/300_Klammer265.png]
Hilfswerkzeug Klammer 265 mm
   
_Bild 12: Hilfswerkzeug Klammer 265 mm_   

# Hilfswerkzeug Bohrhilfe 0,8 mm
__Freecad-Datei__: [Bohrhilfe_klein_251114.FCStd](/fab/3d/Bohrhilfe_klein_251114.FCStd)   
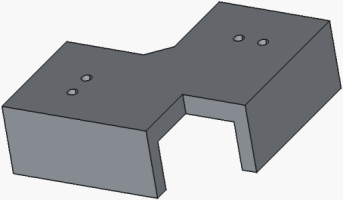
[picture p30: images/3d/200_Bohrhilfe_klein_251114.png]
Bohrhilfe klein 0,8 mm
   
_Bild 13: Hilfswerkzeug Bohrhilfe klein 0,8 mm_   

# Leerer Vorderteil eines 25 cm-Moduls
__Freecad-Datei__: [Rahmen_Front_S__230mm_261008.FCStd](/fab/3d/Rahmen_Front_S__230mm_261008.FCStd)   
Rahmen_Front_S__230mm_261008   
_Bild 14: Leerer Vorderteil eines 25 cm-Moduls_   

# Standard-Vorderteil eines 25 cm-Moduls
__Freecad-Datei__: [Rahmen_Front_S_Oled_34_230mm_260906.FCStd](/fab/3d/Rahmen_Front_S_Oled_34_230mm_260906.FCStd)   
Rahmen_Front_S_Oled_34_230mm_260906   
_Bild 15: Standard-Vorderteil eines 25 cm-Moduls_   

# Rückseite mit P2-Stecker-Ausnehmung eines 25 cm-Moduls
__Freecad-Datei__: [Rahmen_Back_N__2xP20_230mm_261008.FCStd](/fab/3d/Rahmen_Back_N__2xP20_230mm_261008.FCStd)   
Rahmen_Back_N__2xP20_230mm_261008   
_Bild 16: Rückseite mit P2-Stecker-Ausnehmung eines 25 cm-Moduls_   

[Zum Seitenanfang](#up)

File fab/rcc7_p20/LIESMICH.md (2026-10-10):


<table><tr><td></td><td>
<h1>20-polige Verbindungskabel</h1><b><big>RCC7: Flachbandkabel statt Sub-D-Kabel</big></b><br>  
Stand: 25.8.2026    &nbsp; &nbsp; &nbsp; &nbsp;
<a href="#TableOfContents">→ Inhaltsverzeichnis</a>&nbsp; &nbsp; &nbsp; &nbsp;
<a href="README.md">→ English version</a>
</td></tr></table>

# Worum geht es?
Nach **NEM 908D** werden Eisenbahn-Module mit **SUB-D-25-Steckverbindern** nach DIN 41652 und Leitungen mit einem Querschnitt von mindestens **1 mm²** verbunden.

Die Herstellung dieser Kabel ist jedoch **aufwändig und zeitintensiv**.

Für wenige Module mit einer kleinen Anzahl von Zügen können auch **20-polige Flachbandkabel** verwendet werden. Bei zwei parallel geschalteten Adern mit jeweils **0,09 mm²** sollte der Strom **1,5 A nicht überschreiten**.

Dieses Kapitel beschreibt Komponenten für eine **Verdrahtung mit 20-poligen Kabeln**.

##  Inhalt
1. [Verbindung Sub-D-Stecker auf Wannenstecker `CON_20_SubD_*`](#x10)   
2. [Wannenstecker auf Schraubklemmen](#x20)   
3. [Wannenstecker mit Netzteil](#x30)   

# 1. Verbindung Sub-D-Stecker auf Wannenstecker

## 1.1 Einleitung

Für den Übergang vom 25-poligen Sub-D-Stecker auf den 20-poligen Wannenstecker gibt es vier Varianten:  

(A) **2x Sub-D-Stecker auf zwei Wannenstecker** (`PCB_F_CON_20_2x_2xSubD_V1`)  
(B) Sub-D-Stecker WEST auf Wannenstecker (`CON_20_SubD_W`)  
(C) Sub-D-Stecker OST auf Wannenstecker (`CON_20_SubD_O`)  
(D) Sub-D-Stecker OST **ausgekreuzt** auf Wannenstecker (`CON_20_SubD_OX`)  

## 1.2 2x Sub-D-Stecker auf zwei Wannenstecker

rcc7_CON_20_2x_2xSubD_V1_assembled   

### Schaltplan
rcc7_CON_20_2x_2xSubD_V1_circuit   

### Bestückung
rcc7_CON_20_2x_2xSubD_W_V1_pcb   

1. Wannenstecker J2, J3  
2. Sub-D Stecker J1, J4  
3. Draht J5-J6 und J7-J8  

### Versionen
* V1 (260825): OK  

## 1.3 Sub-D-Stecker WEST auf Wannenstecker (`CON_20_SubD_W`)

### Schaltplan
rcc7_CON_20_SubD_W_V1_circuit   

### Bestückung
rcc7_CON_20_SubD_W_V1_pcb   

1. Draht J3-J4  
2. Wannenstecker J5  
3. Sub-D Stecker J1  

### Versionen
* V1 (260820): OK  

## 1.4 Sub-D-Stecker OST auf Wannenstecker (`CON_20_SubD_O`)

### Schaltplan
rcc7_CON_20_SubD_O_V1_circuit   

### Bestückung
rcc7_CON_20_SubD_O_V1_pcb   

1. Wannenstecker J2  
2. Sub-D Stecker J1  
3. Draht J3-J4  

### Versionen
* V1 (260820): OK  

## 1.5 Sub-D-Stecker OST ausgekreuzt auf Wannenstecker (`CON_20_SubD_OX`)

### Schaltplan
Die Schaltung entspricht der OST-Schaltung, lediglich der Wannenstecker ist um 180° verdreht.  

### Bestückung
rcc7_CON_20_SubD_OX_V1_pcb   

1. Wannenstecker J2  
2. Sub-D Stecker J1  

### Versionen
* V1 (260820): OK  

# 2. Wannenstecker auf Schraubklemmen

## 2.1 Einleitung

Für den Übergang vom 20-poligen Wannenstecker auf Schraubklemmen gibt es drei Varianten:  
(A) **Drei Wannenstecker mit allen Schraubklemmen auf einer Seite** (`PCB_F_CON_20_3x_Screw10`)  
(B) Wannenstecker mit allen Schraubklemmen auf einer Seite (`CON_20_Screw10`)  
(C) Wannenstecker mit 6 und 4 Schraubklemmen (`CON_20_Screw64`)  

## 2.2 Drei Wannenstecker mit allen Schraubklemmen auf einer Seite (`PCB_F_CON_20_3x_Screw10`)

rcc7_CON_20_3x_Screw10_V1_assembled rcc7_CON_20_Screw10_V1_assembled   

### Schaltplan
rcc7_CON_20_3x_Screw10_V1_circuit rcc7_CON_20_Screw10_V1_circuit   

### Bestückung
rcc7_CON_20_3x_Screw10_V1_pcb   

Wird das Board auf der **Nordseite** eines Moduls verwendet, so wird es folgendermaßen bestückt:   
1. Wannenstecker J1 und J7 auf die **Lötseite**  
2. Wannenstecker J8 auf die **Bauteilseite**  
3. Schraubklemmen J2 bis J6 auf die **Bauteilseite**  

### Versionen
* V1 (261006): OK  

## 2.3 Wannenstecker mit allen Schraubklemmen auf einer Seite (`CON_20_Screw10`)  

### Schaltplan
rcc7_CON_20_Screw10_V1_circuit   

### Bestückung
rcc7_CON_20_Screw10_V1_pcb   

1. Wannenstecker J1  
2. Schraubklemmen J2 bis J6  

### Versionen
* V1 (261006): OK  

## 2.4 Wannenstecker mit 6 und 4 Schraubklemmen (`CON_20_Screw64`)  

### Schaltplan
Der Schaltplan ist ähnlich wie bei `CON_20_Screw10`, lediglich bei J2 und J6 ist die Verdrahtung vertauscht.  
rcc7_CON_20_Screw64_V1_circuit   

### Bestückung
rcc7_CON_20_Screw64_V1_pcb   

1. Wannenstecker J1  
2. Schraubklemmen J2 bis J6  

### Versionen
* V1 (260820): OK  

# 3. Wannenstecker mit Netzteil

## 3.1 Einleitung

Für den Wannenstecker mit Netzteil gibt es zwei Varianten:  

(A) Wannenstecker mit Netzteil (`CON_20_2x6pol`)  
(B) Zwei Wannenstecker mit Netzteil (`CON_20_2x_2x6pol`)  

## 3.2 Wannenstecker mit Netzteil (`CON_20_2x6pol`)  

### Schaltplan
rcc7_CON_20_2x6pol_V1_circuit   

### Bestückung
rcc7_CON_20_2x6pol_V1_pcb   

1. Wannenstacker J4 (20-polig) auf die **Lötseite** der Platine (auf Polung achten)  
2. Leistungswiderstand R1  
3. Diode D1 (auf Polung achten)  
4. 8-polige Stiftleisten J3, J5 und J6  
5. 6-polige Wannenstecker J1, J2 (auf Polung achten)  
6. Schraubklemmen J7 (grün)  
7. Schraubklemmen J8, J9 (schwarz)  
8. Elko C1  

### Versionen
* V1 (260820): Bild von J7 auf Siebdruck-Bauteilseite um 180° verdreht. Funktion OK.  
* V2 (260827): OK

[Zum Seitenanfang](#up)

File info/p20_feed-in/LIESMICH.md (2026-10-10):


<table><tr><td></td><td>
<h1>P20 Feed-In</h1><b><big>Modul-Einspeisung mit 20-poligen Flachbandkabeln</big></b><br>  
Stand: 7.10.2026    &nbsp; &nbsp; &nbsp; &nbsp;
<a href="#TableOfContents">→ Inhaltsverzeichnis</a>&nbsp; &nbsp; &nbsp; &nbsp;
<a href="README.md">→ English version</a>
</td></tr></table>

## Worum geht es?

Gemäß [NEM 908](https://github.com/khartinger/RCC5V/tree/main/info/con_NEM908/LIESMICH.md) werden Eisenbahn-Module über 10- bis 13-polige Kabel und 25-polige Sub-D-Buchsen miteinander verbunden. Die Verbindung erfolgt durch die Seitenteile der Module.

### Nachteile

* Die Kabel sind aufwendig zu löten (Sub-D-Buchsen).
* Bei Modulen, die auf einer Unterlage stehen, ist das Abstecken der Stecker schwierig, da das Modul-Innenleben ohne Anheben der Module nicht zugänglich ist.  

Aus diesem Grund wird hier eine **alternative Modulversorgung mit 20-poligen Flachbandkabeln** vorgestellt. Diese Verbindung wird im Folgenden als **„P20“** bezeichnet.  
**„P20“** ist nur für **Zweileitersysteme** geeignet, da keine Adern zur Mittelleiterversorgung vorgesehen sind. Für Dreileitersysteme müsste man das P20-System mit 26-poligen Steckern realisieren.  

##  Inhalt
1. [Flachbandkabel, Buchsen und Stecker](#x10)   
2. [P20-Boards](#x20)   

# 1. Flachbandkabel, Buchsen und Stecker

## 1.1 Pinbelegung

Jede Ader eines Flachbandkabels hat einen Querschnitt von **0,08 bis 0,09 mm² (AWG 28)** und kann mit maximal **1 A** belastet werden. Werden alle Adern gleichzeitig belastet, muss der zulässige Strom aufgrund der Erwärmung des Kabels auf etwa **0,4 bis 0,7 A pro Ader** reduziert werden.  

Im **P20-System** werden daher jeweils **zwei Adern parallel geschaltet**:

P20_pins  

_Vorteil_: Stecker kann auf die Bauteilseite **oder** Lötseite gelötet werden.  

## 1.2 Montage auf dem Modul-Rahmen
Üblicherweise werden immer zwei Wannenstecker nebeneinander parallel geschaltet. Der Pin-Abstand beträgt dabei 0,4" = 10,16 mm.  
In der Rückwand des Rahmens wird folgende Öffnung benötigt:  
Loch Wannenstecker  

# 2. P20-Boards

## 2.1 Modulanschlüsse
Es gibt zwei Arten:  
* 20-poliger Stecker auf Schraubklemmen  
* 20-poliger Stecker auf Netzteilplatine  

### 2.1.1 20-poliger Stecker auf Schraubklemmen
Das Board `CON_20_3x_Screw10_V1` wird verwendet, wenn das Modul keine Blöcke hat und lediglich die Fahrspannung und eventuell Licht etc. benötigt werden.  

![]()   

Der Bau ist []() beschreiben.  

### 2.1.2 20-poliger Stecker auf Netzteilplatine
Das Board `CON_20_2x_2x6pol_R_V2` erzeugt die 5V-Spannung und stellt die 6-poligen POWER- und DCC- Anschlüsse zur Verfügung. Der Fahrstrom ist auf Schraubklemmen herausgeführt.  

## 2.2 Umsetzung auf Sub-D-Stecker
Dazu gibt es zwei Varianten  
* 20-poliger Stecker auf einen Sub-D-Stecker
* 20-poliger Stecker auf zwei Sub-D-Stecker

### 2.2.1 20-poliger Stecker auf einen Sub-D-Stecker

### 2.2.2 20-poliger Stecker auf zwei Sub-D-Stecker
Diese Variante wird zB innerhalb von Modulen verwendet

[Zum Seitenanfang](#up)

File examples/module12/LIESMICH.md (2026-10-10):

<table><tr><td></td><td>
Letzte &Auml;nderung: 17.2.2025 <br>   
<h1>Bau des Moduls 12 "Ausweichstelle und Abstellgleis"</h1>
<a href="README.md">==> English version</a>&nbsp; &nbsp; &nbsp; 
</td></tr></table>   

[Hier geht es direkt zur Inhalts&uuml;bersicht](#x05)   

# &Uuml;bersicht
Diese Anleitung beschreibt den Bau eines 100 x 25 cm² gro&szlig;en N-Spur-Gleis-Moduls M12 „Ausweichstelle und Abstellgleis“. Das Bild zeigt das technisch fertige Modul ohne Landschaftsgestaltung. An der Forderfront erkennt man die Bedien- und Anzeigeelemente f&uuml;r den Handbetrieb.   

Modul M12   
_Bild 1: Rahmen mit Grundplatte und Gleisen._   

## Eigenschaften des Moduls
| | | 
|---|---|
| Modulgröße | 100 x 25 cm² | 
| Gleismaterial  | Fleischmann Spur-N-Gleis mit und ohne Schotterbett | 
| Gleisbild | 1x Dreiwegweiche, 2x Zweiwegweiche, 1x Entkuppler, 4x abschaltbarer Gleisabschnitt | 
| Elektrischer Anschluss | 2x 25-poliger SUB-D-Stecker (entsprechend NEM 908D, je 1x WEST und OST) | 
| Fahrstrom | Analog- oder DCC-Betrieb | 
| Steuerung der Schaltkomponenten | * H&auml;ndisch direkt an der Modulvorderseite <br> * &uuml;ber DCC <br> * durch MQTT-Nachrichten (&uuml;ber WLAN) | 
| Bedienelemente mit R&uuml;ckmeldung | 1x OLED-Display und Taster <br> 1x Dreiwegweiche (Block W3, DCC 121 und 122) <br> 2x Zweiwegweiche (Block W2, DCC 123 und 128) <br> 1x Entkuppler (Block 1OUT, DCC 124) <br> 4x Fahrstrom (Block 2IO, DCC 125, 126, 127 und 129) | 
| WLAN | SSID: &nbsp; &nbsp; &nbsp; `Raspi11` <br> Passwort: `12345678` | 
| MQTT: IP-Adresse des Brokers (Host) | `10.1.1.1` | 
| Sonstiges | * Einfaches Verbinden mit anderen Modulen durch ausziehbare Gleise an den Segment-Enden | 

# Inhaltsverzeichnis   
* [1. Vorbereitung und Einkauf](#x10)   
* [2. Bau des Modul-Rahmens](#x20)   
* [3. Aufbau des Gleisplans](#x30)   
* [4. Elektrische Verdrahtung des Moduls](#x40)   
* [5. Steuerungssoftware](#x50)   
* [6. Probebetrieb](#x60)   
* [7. Abschlie&szlig;ende Arbeiten](#x70)   

[Zum Seitenanfang](#up)   

# 1. Vorbereitung und Einkauf
## 1.1 Entwurf des Gleisplans
### 1.1.1 Allgemeines zu Gleispl&auml;nen
Beim Erstellen eines Gleisplans sind zwei Dinge zu beachten: das Lichtraumprofil und die H&ouml;he des Gleisaufbaus.   
Das __Lichtraumprofil__ gibt an, wieviel Platz (vor allem von langen Waggons) neben dem Gleis ben&ouml;tigt wird. Dies ist vor allem bei engen Radien wichtig.   
F&uuml;r den Radius R2 ben&ouml;tigt man eine Gesamt-Gleisbreite von 27 + 2 · 7 = 41 mm.   
Lichtraumprofil   
_Bild 2: Lichtraumprofil_   

Die __H&ouml;he des Gleisaufbaus__ (Bahnk&ouml;rper) ist f&uuml;r die Landschaftsgestaltung und bei mehrst&ouml;ckigen Anlagen oder Tunnels wichtig. Man kann verschiedene Ebenen unterscheiden.   
* E0 . . . . . Oberkante der Basisplatte (= 6 cm &uuml;ber einer Tischplatte). Auf dieser Ebene werden der Bahndamm und, darauf aufbauend, das Schotterbett aufgesetzt.   
* E5 . . . . . Oberkante des Bahndamms. Auf dieser Ebene setzt das Schotterbett auf.   
* E8 . . . . . Auf dieser Ebene liegt das Modellgleis. Hier werden auch Modell-Bahnsteige und Bahnh&ouml;fe platziert. In der Realit&auml;t gibt es diese Ebene eigentlich nicht, da sie mitten in der H&ouml;he des Schotterbettes liegt.   
* E10 . . . . . Oberkante des Schotterbettes bzw. Unterkante des Gleises.   
* E12 . . . . . Oberkante des Gleises. Stra&szlig;en f&uuml;r Bahn&uuml;bersetzungen sollten dieses Niveau haben, wobei Bahn&uuml;bergang-Baus&auml;tze oft eine Art "Rampe" bzw. Auffahrt haben, weil die Baus&auml;tze &uuml;blicherweise auf Ebene E8 platziert werden.   

Aufbau Bahnk&ouml;rper   
_Bild 3: Aufbau des Bahnk&ouml;rpers_   

Im Modell wird der Bahnk&ouml;rper aus 5 mm Sperrholz und 3 mm Schaumstoff der Fa. Noch (95962 Gleisbett-Rolle N) hergestellt und mit Gleisschotter der Firma Fleischmann (9479) verfeinert. Mit einer H&ouml;he von 4 mm (genauer 4,1 mm) f&uuml;r das Fleischmann-Gleis mit Schotterbett ergibt sich eine Gesamth&ouml;he von 12,1 mm.   
Sollte 5 mm Sperrholz nicht zur Verf&uuml;gung stehen, kann man auch 4 mm starkes Sperrholz verwenden und auf die Unterseite einen ein Millimeter dicken, selbst klebenden Kork hinaufkleben.   
Wenn man die __Breite des Bahndamms__ (Planum) mit 40 mm (oben) bzw. __50 mm__ (unten) annimmt, so ist das Lichtraumprofil f&uuml;r R2 in der Breite automatisch erf&uuml;llt.   
__Mindesth&ouml;he im Tunnel__: 46 mm (H&ouml;he ab Schwellenunterkante) + 3 mm (Schotterbett) + 5 mm (Bahndamm) = __54 mm__ ab der Grundplatte.   

### 1.1.2 Entwurf des Gleisplans
Der Entwurf des Gleisplans erfolgt in zwei Schritten:   
* Zuerst wird der Gleisplan so entworfen, dass er grunds&auml;tzlich den Anforderungen entspricht.   
* Im n&auml;chsten Schritt wird die Lage der Stromversorgungsstellen und Isolationsstellen festgelegt. Das kann dazu f&uuml;hren, dass zB Gleise in zwei Teile zerlegt werden m&uuml;ssen, damit man 2-polige Anschlusskabel (Fleischmann 22217) oder Isolierschienenverbinder (Fleischmann 9403) anbringen kann.   

Der folgende Gleisplan wurde mit dem Programm [AnyRail](https://www.anyrail.com/) gezeichnet.   
M12 Gleisplan   
_Bild 4: Gleisplan_   

Dunkelgraue Dreiecke stellen Gleisisolierungen dar (Isolierschuhe), braune und rote Kreise sind Fahrstromeinspeisungen.   
Das 2. Gleis von links ist ein Gleis ohne Schotterbett mit der L&auml;nge 17,2 mm (22207). Die &uuml;brigen kurzen Gleise sind Gerade (9104) mit der L&auml;nge 27,75 mm. (Im Plan schlecht lesbar.)   
Eine Besonderheit stellt das Gleis 9136 mit dem Kommentar "R4 9 Schwellen" dar: Hier wird ein Gleis 9136 zuerst links mit der Weiche verbunden und danach bei einem Winkel von 6,14° (= 9 Schwellen) "abgeschnitten".   

## 1.2 Schienenkauf - St&uuml;ckliste
Zum Bau des Moduls werden folgende Gleise und Zubeh&ouml;r ben&ouml;tigt:   
| Anzahl | Nummer | Name | Euro/Stk | Euro | 
| :---: | :---: | :--- |  ---: |  ---: |
| 1 | 22207 |  N Fleischmann, Gerade 17,2 mm | 2,00 | 2,00 | 
| 1 | 22210 | N Fleischmann, Aufgleisger&auml;t gerade, 104,2 mm | 4,20 | 4,20 | 
| 8 | 9101 | Gerade 111 mm | 4,40 | 35,20 | 
| 1 | 9102 | Gerade 57,5 mm | 4,40 | 4,40 | 
| 1 | 9103 | Gerade 55, 5 mm | 4,40 | 4,40 | 
| 9 | 9104 | Gerade | 4,40 | 39,60 | 
| 2 | 9110 | Ausgleichsgleis gerade 83mm-111mm | 14,60 | 29,20 | 
| 1 | 9112 | Entkupplungsgleis gerade (mit Antrieb) | 31,90 | 31,90 | 
| 2 | 9116 | Prellbock 57,5 mm | 8,40 | 16,80 | 
| 1 | 9135 | Bogen Radius 430mm, Winkel 30° (R4) | 4,90 | 4,90 | 
| 3 | 9136 | Bogen Radius 430mm, Winkel 15° (R4) | 4,90 | 14,70 | 
| 1 | 9157 | Dreiwegweiche | 47,80 | 47,80 | 
| 1 | 9178 | Weiche links mit stromleitendem Herzst&uuml;ck | 29,90 | 29,90 | 
| 1 | 9179 | Weiche rechts mit stromleitendem Herzst&uuml;ck | 29,90 | 29,90 | 
| 4 | 640000 | Elektromagnetischer Weichenantrieb mit Endabschaltung | 25,60 | 102,40 | 
| 1 | 9403 | Isolierschienenverbinder | 6,90 | 6,90 | 
| 7 | 22217 | 2-poliges Anschlusskabel | 4,40 | 30,80 | 
   
Gesamtkosten 2025: ca. 435 Euro   

## 1.3 Rahmen
### 1.3.1 Modulrahmen
Der 100 x 25 cm² gro&szlig;e Modulrahmen ist 6 cm hoch und besteht aus zwei Seitenteilen ("Ost" und "West"), zwei L&auml;ngsteilen ("Nord" und "S&uuml;d") sowie drei Querstreben. Die Gel&auml;ndeplatte wird in den Rahmen eingelegt.   
Die Teile des Rahmens k&ouml;nnen entweder aus Holz hergestellt oder mit dem 3D-Drucker gedruckt werden. Auch eine gemischte Bauweise ist m&ouml;glich, zB Seitenteile und Querstreben 3D-Drucken, L&auml;ngsteile aus Holz.   

### 1.3.2 Holzkauf f&uuml;r Modul 100 x 25 cm²
Das Holz besorgt man sich am besten bei einem Baumarkt und l&auml;sst es gleich auf die folgenden Gr&ouml;&szlig;en zuschneiden:   

__Pappelsperrholz 10 mm__   
| St&uuml;ck | Abmessung | Kurzbezeichnung | Verwendung | 
|:-----:|:---:|:---:|:---|
| 1 | 980 x 230 mm² | - | Gel&auml;nde-Grundplatte | 
| 2 | 980 x 60 mm²  | Ra2, Ra4 | Rahmen au&szlig;en Nord, S&uuml;d | 
| 2 | 250 x 70 mm²  | Ra1, Ra3 | Rahmen au&szlig;en West, Ost | 
| 3 | 230 x 50 mm²  | Ri1 | Rahmen innen | 

__Pappelsperrholz 5 mm (oder 4 mm)__   
| St&uuml;ck | Abmessung | Anmerkung | 
|:-----:|:---:|:---|
| 1 | 980 x 250 mm² | Bahndamm  | 

__Kleinteile__   
4x Pappelsperrholz 10 mm stark, 70 x 35 mm² f&uuml;r die Halterungen der Sub-D-Stecker.   
4x kleine Holzst&uuml;cken 10 x 10 x 50 mm³ als zus&auml;tzliche Auflager f&uuml;r die Grundplatte.   
20x Schraube M3 x 30 mm Senkkopf, Kreuzschlitz, selbstschneidend (zB Fa. Spax 4 003530 021251)   
8x Schraube M 2,5 x 16 mm Kreuzschlitz, Senkkopf   
8x Sechskantmutter M 2,5 mm   
4x Schraube M 3 x 35 mm Kreuzschlitz, Halbrundkopf   
4x Sechskantmutter M 3 mm   

## 1.3.3 Verbrauchsmaterial
Zum Bau des Moduls wird noch folgendes ben&ouml;tigt:   
| St&uuml;ck | Nummer | Lieferant  | Bezeichnung | 
|:---:|:---:|:---|:---|
| 1 | | Ponal | Holzleim Express | 
| 1 |  95962 | Noch | Gleisbett-Rolle N 730 cm lang, 3,2 cm breit, 0,3 cm stark | 
| 1 | | [Amazon](https://www.amazon.de/dp/B07S188DRJ?ref=ppx_yo2ov_dt_b_product_details&th=1) | Selbstklebende Korkplatte 1 mm dick, 30 x 21 cm² | 
| 28 | | | Senkkopfschrauben mit Kreuzschlitz 3,0 x 30mm | 

Damit der Holzrahmen nicht so leicht verstaubt, sollte er lackiert werden. Dazu ben&ouml;tigt man:   
| St&uuml;ck | Nummer | Lieferant  | Bezeichnung | 
|:---:|:---:|:---|:---|
| 1 | 4002364114016 | Albrecht | Yacht- und Bootslack, farblos, hochgl&auml;nzend | 
| 1 | | | Topfreiniger (Abwasch-Schwamm) | 
| 2 | | | Paar Einmal-Handschuhe | 
| 1 | | | Schleifpapier K&ouml;rnung 240 | 

## 1.4 Elektronische RCC-Komponenten
### 1.4.1 Steuerung
Die Steuerung besteht aus einem ESP32 mit zwei Zusatzplatinen (I²C, DCC) und dem 1,54"-OLED-Display. Der Zusammenbau ist auf   
[`https://github.com/khartinger/RCC5V/blob/main/fab/rcc2_esp32/LIESMICH.md`](/fab/rcc2_esp32/LIESMICH.md)   
beschrieben.   
OLED_Shields_uC   
_Bild 5: Zusammengebaute Steuerung aus OLED, Shields und Mikrocontroller ESP32_   

### 1.4.2 Anschluss der 25-poligen Stecker
F&uuml;r den Anschluss der 25-poligen Stecker und f&uuml;r die Stromversorgung werden folgende best&uuml;ckte Leiterplatten ben&ouml;tigt:   
* 1x [Netzteil-Platine AC_5V_supply_6pol_DCC](/fab/rcc1_supply/LIESMICH.md#x20)   
* 1x [Platine mit 25-poligem Sub-D-Stecker, Schraubklemmen und Netzteil (RW_5V_SUB25_10)](/fab/rcc1_supply/LIESMICH.md#x33)   
* 1x [Platine mit 25-poligem Sub-D-Stecker und Schraubklemmen (CON_SubD_Screw10)](/fab/rcc1_supply/LIESMICH.md#x34)   

Die best&uuml;ckte Netzteil-Platine muss auf die Tr&auml;gerplatine `RW_5V_SUB25_10` montiert werden.   

Sub-D-Stecker mit Netzteil   
_Bild 6: Sub-D-Stecker f&uuml;r West und Ost_   

### 1.4.3 Ansteuerung der Schaltkomponenten
F&uuml;r die Ansteuerung der Schaltkomponenten werden folgende Schaltbl&ouml;cke ben&ouml;tigt:   
* 8x [Halterung f&uuml;r Schaltbl&ouml;cke](/fab/rcc5_add_ons/LIESMICH.md#x20)   
* 1x [Block Dreiwegweiche (W3)](/fab/rcc4_block/LIESMICH.md#x30)   
* 2x [Block Zweiwegweiche (W2)](/fab/rcc4_block/LIESMICH.md#x20)   
* 1x [Block Entkuppler (1OUT)](/fab/rcc4_block/LIESMICH.md#x40)   
* 4x [Block Abschaltbares Gleis (2IO)](/fab/rcc4_block/LIESMICH.md#x50)   

M12_Schaltbl&ouml;cke   
_Bild 7: Schaltbl&ouml;cke f&uuml;r das M12-Modul: W3, 2x W2, 1OUT und 4x 2IO (hinten)_   

Weiters werden 3 + 2x2 + 3 + 4x5 = 30 LED-Fassungen ben&ouml;tigt.   

LED-Fassungen   
_Bild 8: LED-Fassungen_   

### 1.4.4 I²C-Expander
* 4x [PCF8574 I/O-Expander (Adresse 0x20 bis 0x23)](/fab/rcc0_start/LIESMICH.md#34)   
* 3x [Halterung 20 mm f&uuml;r I/O-Expander](/fab/rcc3_i2c/LIESMICH.md#20)   
* 1x [Halterung mit Abschlusswiderst&auml;nden](/fab/rcc3_i2c/LIESMICH.md#60)   

M12_I2C_IO   
_Bild 9: I²C-I/O-Expander f&uuml;r das M12-Modul_   

### 1.4.5 Zusatzplatinen f&uuml;r die Verdrahtung
Zum Anschluss der Schaltkomponenten sinnvoll sind folgende Zusatzplatinen:   
* 8x [`CON_10pol_PIN` oder `CON_10pol_2x4` Umsetzer 10-poliges Kabel auf Stifte](/fab/rcc5_add_ons/LIESMICH.md#x30)   
* 2x [`CON_1xIO` Fahrstromschalter einfach](/fab/rcc5_add_ons/LIESMICH.md#x70)   
* 3x [`CON_6pol_3` 6-poliger Stecker auf drei Schraubklemmen](/fab/rcc5_add_ons/LIESMICH.md#x40)   
* 2x [`CON_6pol_6` 6-poliger Stecker auf sechs Schraubklemmen](/fab/rcc5_add_ons/LIESMICH.md#x50)   
* 1x [`CON_2xIO` Fahrstromschalter doppelt](/fab/rcc5_add_ons/LIESMICH.md#x80)   
* 1x [`CON_2pol_141` Fahrstromverteiler](/fab/rcc5_add_ons/LIESMICH.md#x60)   

M12_ADD_ON   
_Bild 10: Add-on-Boards f&uuml;r das M12-Modul_   

__Dr&auml;hte, Leitungen und Stecker__   
* ca. 4 m Volldraht 22awg (0,32 mm²) rot   
* ca. 4 m Volldraht 22awg (0,32 mm²) braun   
* ca. 3 m Flachbandkabel 6-polig   
* ca. 2 m Flachbandkabel 10-polig   
* ca. 60 cm 10-poliges Kabel 10 x 1 mm²   
* 4x 10-poliges Flachbandkabel mit Buchsen Female-Female 10 cm lang (Dupont Jumper Wire Cable)   
* 1x 10-poliges Flachbandkabel mit Buchsen Female-Female 15 cm lang (Dupont Jumper Wire Cable)   
* 2x vier Kabel Male-Female 30 cm lang (orange, gelb, gr&uuml;n, blau)   
-----   
* 28x IDC Buchsen-Stecker f&uuml;r Flachbandkabel 6-polig   
* 16x IDC Buchsen-Stecker f&uuml;r Flachbandkabel 10-polig   
* 8x L&uuml;sterklemmen   

[Zum Seitenanfang](#up)   

# 2. Bau des Modul-Rahmens   
## 2.1 Einleitung
Jedes Modul besteht aus einem Rahmen mit Querverbindungen und der Grundplatte, die die Gleise und Landschaft tr&auml;gt. Zuerst erstellt man den Modul-Rahmen. Das hat zwei Vorteile:   
1. Der Test, ob die Grundplatte in den Rahmen passt, kann mit der leeren Grundplatte erfolgen. Falls die Grundplatte zu gro&szlig; ist, kann sie einfach zugeschnitten oder zugeschliffen werden.   
2. Beim Aufkleben der Gleise auf die Grundplatte sind an den Modul&uuml;berg&auml;ngen (Ost und West) bereits die Seitenteile mit den Gleisausnehmungen vorhanden. So sind die Gleise beim Aufkleben sicher an der richtigen Position.   

Das folgende Bild zeigt den Grundriss des Modulrahmens:   

Modul-Rahmen   
_Bild 11: AnyRail-Darstellung des Rahmengrundrisses mit den Au&szlig;enteilen (Ra1 bis Ra4) und Querverstrebungen (Ri1 bis Ri3)_

Die einzelnen Teile des Rahmens m&uuml;ssen vor dem Zusammenbau entspechend den nachfolgenden Beschreibungen bearbeitet werden.   

## 2.2 Seitenteile Ra1, Ra3 (West, Ost)
Die Seitenteile sind an eine (ehemalige?) Norm von n-spur.at angelehnt, wobei das Bahnk&ouml;rper-Profil aber der NEM122 entspricht:   

Modul_OstWest_1_Mitte   
_Bild 12: Ma&szlig;e f&uuml;r die Seitenteile Ost und West (Modulbreite 250mm, ein in der Mitte liegendes Gleis)._   

* Ausgangsmaterial: Pappelsperrholzplatte 10 mm, 250 x 70 mm²   
* Die vier 8mm-Bohrungen dienen zum Verbinden der Module mit 8 mm-Fl&uuml;gelschrauben und Fl&uuml;gelmuttern.   
* Die linken und rechten vier 2 mm-Bohrungen dienen zum Anschrauben der Nord- und S&uuml;dwand. Sie m&uuml;ssen mit einem Kegelsenker erweitert werden, damit die Senkkopfschrauben nicht vorstehen.   
* Die oberen zwei 2mm-Bohrungen dienen zum Fixieren der Gel&auml;nde-Grundplatte (falls erforderlich). Auch sie m&uuml;ssen mit einem Kegelsenker erweitert werden, damit die Senkkopfschrauben nicht vorstehen.   
* Die 60x20 mm²-Ausnehmung dient zum Durchf&uuml;hren des 25-poligen Sub-D-Steckers.   

Mit besonderer Vorsicht ist die Ausnehmung f&uuml;r das Gleis zu fertigen. Mit einer Laubs&auml;ge wird die Ausnehmung etwas zu klein ausgeschnitten und mit einer Dreiecksfeile so lange erweitert, bis ein Fleischmann-Schotterbett-Gleis gerade (klemmend) hineinpasst und auch mittig positioniert ist.   

## 2.3 Rahmenteil Ra2 (Nord)
Der Rahmenteil „Nord“ enth&auml;lt lediglich dreimal zwei Bohrungen mit 2 mm Durchmesser, die wieder mit einem  Kegelsenker erweitert werden. Hier werden innen die Querverstrebungen verschraubt.   

Modul_Nord_980mm   
_Bild 13: Seitenteil Nord Ra2_   

## 2.4 Rahmenteil Ra4 (S&uuml;d)
Der Rahmenteil S&uuml;d ist am aufw&auml;ndigsten zu fertigen, da er das Display, einen Taster und die Bohrungen f&uuml;r alle Steuerbl&ouml;cke und f&uuml;r alle Querverstrebungen enth&auml;lt. Das folgende Bild gibt einen &Uuml;berblick &uuml;ber die erforderlichen Bohrungen.   

Modul_S&uuml;d_980mm   
_Bild 14: Ma&szlig;e f&uuml;r den Rahmenteil S&uuml;d (Ra4)_   

__OLED-Anzeige__   
Die Aussparungen f&uuml;r die OLED-Anzeige und den dazugeh&ouml;rigen Taster sind abh&auml;ngig davon, ob man die Bauteile einzeln montiert oder einen 3D-Druck-Rahmen verwendet. Bei getrennter Montage ben&ouml;tigt man eine rechteckf&ouml;rmige Aussparung der Gr&ouml;&szlig;e 20 x 38 mm² und eine 11,6 mm-Bohrung.   
OLED_Button_single   
_Bild 15: Ma&szlig;e f&uuml;r die getrennte Montage der OLED-Anzeige und des Tasters_   

Bei Verwendung eines 3D-gedruckten Rahmens ben&ouml;tigt man eine rechteckf&ouml;rmige Aussparung der Gr&ouml;&szlig;e 80 x 43 mm².   
OLED_Button_frame   
_Bild 16: Ma&szlig;e f&uuml;r den Rahmen der OLED-Anzeige mit Taster_   

__Steuerbl&ouml;cke__   
Je nach Art des Steuerelementes werden unterschiedliche Bohrungen ben&ouml;tigt. So zeigt das Symbol der Dreiwegweiche W3 nach rechts (6 Bohrungen), das der ersten Zweiwegweiche W2 nach links unten (4 Bohrungen) und das des Entkupplers 1OUT nach rechts (4 Bohrungen). Es folgen die drei Schaltsymbole f&uuml;r die Fahrstromabschaltung 2IO (7 Bohrungen) und das Schaltbild der zweiten Zweiwegweiche W2 nach rechts oben (4 Bohrungen).   
Die genaue Lage aller Bohrungen f&uuml;r einen Schaltblock zeigt das folgende Bild, wobei je nach Schaltblock-Typ nur die entsprechenden Bohrungen ben&ouml;tigt werden (!):   

Bohrposition LEDs und Taster   
_Bild 17: Ma&szlig;e f&uuml;r die LED- und Taster-Bohrungen_   

Der Bohrdurchmesser f&uuml;r die LED-Fassungen betr&auml;gt 5,6 mm, der f&uuml;r die Taster ca. 7 mm.   

Das einzelne Anzeichnen der Positionen der Bohrungen ben&ouml;tigt viel Zeit und genaues Arbeiten. Daher macht es Sinn, f&uuml;r die Schaltbl&ouml;cke Abdeckungen (Beschriftungen) zu entwerfen, diese auf Etikettenpapier auszudrucken und auf das Holz aufzukleben (Abstand zum unteren Rand 8 mm). Damit ist das Bohren wesentlich einfacher. Die Beschriftungen k&ouml;nnen entweder beibehalten oder entfernt werden, wenn man sie nicht m&ouml;chte. Falls die Beschriftungen zu stark durch das Bohren besch&auml;digt wurden, kann man sie auch durch neue ersetzen....   

Das folgende Bild zeigt die 40 x 42 mm gro&szlig;en Abdeckungen.   
 
Beschriftung Bedienungselemente   
_Bild 18: Beschriftung der Bedienungselemente f&uuml;r Modul 12_   

__LED-Fassungen__   
Nach dem Bohren sind die Bohrungen zu reinigen und die LED-Fassungen einzupressen.   

__Halterungen f&uuml;r Steuerbl&ouml;cke__   
Als N&auml;chstes kann man die Halterungen f&uuml;r die Steuerbl&ouml;cke mit 2,6 x 8 mm Schrauben anschrauben. Der Abstand der Bl&ouml;cke von der Unterseite des Rahmens sollte 5,5 mm betragen, allerdings ist die Lage der Halterungen meist durch die LED-Fassungen bereits vorgegeben...   

Die Position der Schrauben f&uuml;r die Steuerblock-Halterungen auf der Innenseite des Rahmens ist folgenderma&szlig;en festgelegt:   
Schraubposition f&uuml;r Blockhalter   
_Bild 19: Position der Schrauben f&uuml;r die Steuerblock-Halterungen_   

Den fertigen Rahmenteil S&uuml;d (ohne Fahrstromabschaltung Gleis 1A) zeigen die folgenden Bilder   
Rahmenteil S&uuml;d Forderseite   
_Bild 20: Rahmenteil S&uuml;d Forderseite_   

Rahmenteil S&uuml;d R&uuml;ckseite   
_Bild 21: Rahmenteil S&uuml;d R&uuml;ckseite_   

## 2.5 Querverstrebung Ri1 bis Ri3
Die Querverstrebungen enthalten verschiedene Durchbr&uuml;che f&uuml;r Kabel und zwei Bohrungen f&uuml;r die Halterung der 25-poligen Sub-D-Stecker.   

Verstrebung   
_Bild 22: Querverstrebungen Ri1 bis Ri3_

## 2.6 Halterung f&uuml;r Sub-D-Stecker
Die Halterung f&uuml;r einen SUB-D-Stecker besteht aus zwei U-f&ouml;rmigen Teilen, die links und rechts an einer Querstrebe angeschraubt werden. Die Teile k&ouml;nnen sowohl aus Holz als auch mit 3D-Druck hergestellt werden. F&uuml;r den Modul M12 werden zwei Halterungen ben&ouml;tigt.   

Sub-D-Halterung   
_Bild 23: Ma&szlig;e der Halterung_   

In jeden U-f&ouml;rmigen Teil werden von unten zwei Kreuzschlitz-Senkkopf-Schrauben M 2,6 x 16 mm eingeschraubt und durch eine 2,5 mm Sechskantmutter gesichert. Die Schrauben dienen zum Festschrauben der Versorgungsplatine.   
Die beiden U-f&ouml;rmigen Halterungen werden mit M3 x 35 mm Schrauben und 3mm Sechskantmutter gegeneinander an einer Querstrebe verschraubt.   

Teile der Sub-D-Halterung   
_Bild 24: Teile der Sub-D-Halterung_   

## 2.7 Zusammenbau des Rahmens
Nachdem alle Teile des Rahmens bearbeitet wurden, kann dieser zusammengeschraubt werden.   

Rahmen Ansicht von unten   
_Bild 25: Zusammengeschraubter Rahmen, Ansicht von unten_   

[Zum Seitenanfang](#up)   

# 3. Aufbau der Gleise   

## 3.1 Stellprobe   
Der Probeaufbau erfolgt auf der 5 mm (bzw. 4 mm) Sperrholzplatte. Dazu wird der Gleisplan im Ma&szlig;stab 1:1 auf diese gezeichnet. Das kann entweder durch Ausdruck des Gleisplans im Ma&szlig;stab 1:1 und &uuml;bertragen auf das Sperrholz erfolgen (zB mit Kohlepapier), oder durch &Uuml;bertragen der Koordinaten auf das Sperrholz und Zeichnen des Gleisplans.   
Entsprechend dem Gleisplanentwurf m&uuml;ssen die Trennstellen in jeweils beiden Schienenstr&auml;ngen hergestellt werden. Dazu werden Fleischmann 9403 Isolier-Schienenverbinder verwendet. Die bisherigen Gleisverbinder werden entfernt und durch die Isolier-Schienenverbinder ersetzt.   
Danach werden die Gleise entsprechend dem Gleisbild zusammengesteckt.   
Beim Probeaufbau sollten auch alle bahnspezifischen Bauwerke (wie Bahnhof, Bahnsteige, Verladerampe) aufgestellt werden, damit man wei&szlig;, wie der Bahnk&ouml;rper (die 5 mm bzw. 4 mm Platte) zugeschnitten werden muss.   
Schlie&szlig;lich wird mit dem l&auml;ngsten Waggon h&auml;ndisch eine Probefahrt durchgef&uuml;hrt und kontrolliert, ob alle Radien, &Uuml;berg&auml;nge etc. passen und keine Geb&auml;ude im Wege stehen.   

## 3.2 Zuschneiden und Aufkleben des Bahndamms auf die Grundplatte   
War die Stellprobe erfolgreich, folgen &Uuml;berlegungen zu den einzelnen Gel&auml;ndeh&ouml;hen.   
* An beiden Seiten des Moduls (Ost und West) ist die Gel&auml;ndeh&ouml;he null (E0). Ausgenommen davon ist der Bahndamm und das Schotterbett des Gleises, das in den Modul f&uuml;hrt.   
* Das Schotterbett liegt auf der Ebene E5 (= 5 mm Sperrholz). Der &Uuml;bergang zu Ebene E0 erfolgt &uuml;ber Schr&auml;gen mit 45 Grad.   
* Die Fleischmann-Gleise liegen auf Niveau E8. Dazu wird auf das 5 mm-Sperrholz das 3 mm hohe Schaumstoff-Gleisbett (Fa. Noch Nr. 95962 oder Kork) aufgeklebt. Der Schaumstoff d&auml;mpft auch etwas das Fahrger&auml;usch (Schallschutz).   
* Bahnhofsgeb&auml;ude, Bahnsteige oder Verladerampen stehen normalerweise auf Niveau E8. An diesen Stellen sollte man das 5 mm-Sperrholz ausschneiden und gleich 8 mm hohes Sperrholz einsetzen und nicht die H&ouml;he schichtweise aufzubauen.   
* Stra&szlig;en, die die Gleise &uuml;berqueren, haben als Oberkante E12.   

Hat man entschieden, wo welche Sperrholz-H&ouml;hen eingesetzt werden, schneidet man die entsprechenden Platten zu und klebt sie auf die Grundplatte. Dazu sollte sich die Grundplatte im Rahmen befinden, damit man den Gleisanschluss am linken und rechten Rand genau herstellen kann.   

Sollen die Weichenantriebe als Unterflurantriebe verbaut werden, m&uuml;ssen noch Aussparungen ausgeschnitten werden.   

Ma&szlig;e der Aussparung f&uuml;r Unterflurantrieb   
_Bild 26: Ma&szlig;e der Aussparung f&uuml;r einen Weichen-Unterflurantrieb._   

Bei einer rechten Weiche bilden sechs Punkte die Ecken der Aussparung mit den Koordinaten P1(11/6), P2(101/6), P3(101/25), P4(81/30), P5(31/30) und P6(11/25). F&uuml;r eine linke Weiche sind die Koordinaten gespiegelt. Der Koordinatenursprung befindet sich in der Mitte des Gleisrandes bei den Weichenzungen (siehe Bild oben).    

Ma&szlig;e der Aussparung Unterflurantriebe W3   
_Bild 27: Ma&szlig;e der Aussparung f&uuml;r die Unterflurantriebe einer Dreiwegweiche._   

Die Ecken der Aussparungen bilden sechs Punkte mit den Koordinaten P1(12/5), P2(100/16), P3(97,5/36), P4(73/37), P5(33/32) und P6(9,5/25). F&uuml;r den zweiten Antrieb der Dreiwegweiche sind die Koordinaten gespiegelt. Der Koordinatenursprung befindet sich in der Mitte des Gleisrandes bei den Weichenzungen (siehe Bild oben).    

Die folgenden beiden Bilder zeigen die verschiedenen Ebenen des Gel&auml;ndes und die Aussparungen f&uuml;r die Weichen. Links vorne und rechts hinten ist das Niveau E0, in der Mitte und hinten (im Bild oben) ist 8 mm hohes Sperrholz (E8).   
Bahndamm2   
Bahndamm   
_Bild 28: Verschiedene Modul-Ebenen_

## 3.3 Bettungsk&ouml;rper (Schotterbett)
Im n&auml;chsten Schritt wird das 3 mm hohe Schaumstoff-Gleisbett (Fa. Noch Nr. 95962 oder Kork) aufgeklebt. Dies erfolgt nicht nur an Stellen, wo sp&auml;ter ein Gleis verl&auml;uft, sondern auch an Stellen, die das gleiche Niveau haben sollen, zB zwischen den Gleisen oder dort, wo sp&auml;ter der Antrieb f&uuml;r den Entkuppler hinkommt.   
Danach bohrt man mit einem 4 mm Bohrer die L&ouml;cher f&uuml;r die Fahrstromzuf&uuml;hrung. Wenn man eine 1:1 Vorlage des Gleisbildes ausgedruckt hat, so kann man diese als Bohrschablone verwenden.   
Das folgende Bild zeigt den Modul mit Schaumstoff-Bett, Ausnehmungen f&uuml;r die Weichenantriebe und die Bohrungen f&uuml;r die Fahrstromzuf&uuml;hrung.   

Schotterbett   
_Bild 29: Grundplatte mit Bahndamm, Gleisbett (schwarz), Bohrungen f&uuml;r Fahrstrom und Weichenausschnitten_   

## 3.4 Vorbereitung der Verdrahtung
### Montage der Schaltbl&ouml;cke   
Bevor die Schienen verlegt werden, sollte die Verdrahtung vorbereitet werden (damit die Gleise nicht besch&auml;digt werden). F&uuml;r ein leichteres Arbeiten entfernt man zuerst die Grundplatte vom Rahmen und montiert die Schaltbl&ouml;cke. Dazu steckt man einen Schaltblock in die Schaltblock-Halterung und schraubt ihn mit vier M2 x 20 mm Schrauben fest (Schrauben nicht zu fest anziehen!).    
Schaltblockmontage   
_Bild 30: Anschrauben der Schaltbl&ouml;cke_   

Weiters montiert man auf die erste und dritte Querstrebe die Halterung f&uuml;r die Sub-D-Stecker. Sollte dabei eine Fahrstromzuf&uuml;hrung genau unter einer Halterung liegen, so muss man die Stromzuf&uuml;hrung nochmals bohren....   

### Montage der Anzeige und des Mikrocontrollers   
Die OLED-Anzeige und den Mikrocontroller, wie bei [Rahmenteil Ra4 (S&uuml;d)](#x24) beschrieben, in den Rahmen einsetzen.   

## Montage der I²C-I/O-Expanderplatinen
1. Segment 2: Montage von zwei I²C-PCF8574-I/O-Expanderplatinen und den Hilfsplatinen `CON_i2c_20mm`. Einstellen der Adressen 0x20 und 0x21 mit Hilfe der Jumper.   
2. Segment 3: Montage von zwei I²C-PCF8574-I/O-Expanderplatinen und den Hilfsplatinen `CON_i2c_20mm`. Einstellen der Adressen 0x22 und 0x23 mit Hilfe der Jumper.   

### Montage der Schraubklemmen   
Um die Verkabelung des Moduls &uuml;bersichtlich zu gestalten, werden 2x2 L&auml;ngslinien (Abstand vom Rand 4 cm und 5,5 cm) gezeichnet, die genau durch die Durchf&uuml;hrungen der Querverbinder f&uuml;hren. In diesem Bereich werden die Kabel gef&uuml;hrt. Nun setzt man die Grundplatte wieder in den Rahmen ein.   
F&uuml;r die Platzierung der Klemmen gilt allgemein:   
* I²C-Komponenten (zB die Prints mit 10-poligem Wannenstecker) werden in der N&auml;he der Schaltbl&ouml;cke montiert (im folgenden Bild oben zu sehen). Die Montage sollte aber nicht zu Nahe an den Schaltbl&ouml;cken erfolgen, damit man im Fehlerfall die Schaltbl&ouml;cke noch leicht abschrauben kann.   
* Fahrstromkomponenten (zB Prints mit 6-poligem Wannenstecker) auf der den Schaltbl&ouml;cken gegen&uuml;berliegenden L&auml;ngsseite ("hinten", im Bild unten) und 
* Weichenanschl&uuml;sse in der N&auml;he der Weichen.   

Das folgende Bild zeigt die montierten Klemmen.   

M12_Verdrahtung_1   
_Bild 31: Schraubklemmen f&uuml;r die Verdrahtung_   

#### Montage der Schraubklemmen etc. im Detail    
1. Beschriften der Bohrungen f&uuml;r die Fahrstromzuf&uuml;hrung:   
   Segment 1: GW-1, GW-2,G1A-1   
   Segment 2: E1, G2-1, G1-1   
   Segment 3: G1-2, G2-2, G3-1   
   Segment 4: GO-1, GO-2   
2. Alle Prints werden mit M2 x 10 mm Schrauben, L&uuml;sterklemmen mit M2,6 x 12 mm Schrauben angeschraubt.   
3. Die Gleise der Ein- und Ausfahrt eines Moduls werden immer direkt mit dem Fahrstrom verbunden. Mit dem Stromverteiler-Print `CON_2pol_141_V1` stehen zus&auml;tzliche Klemmen f&uuml;r die Fahrstromverteilung zur Verf&uuml;gung (Gr&uuml;ner Balken unten im 2. Segment von links)   
4. Die Prints 2x `CON_1xIO_V1` und 1x `CON_2xIO_V1` dienen dem Schalten des Fahrstroms (gemeinsam mit den Schaltbl&ouml;cken `2IO`) (unten im Bild 21).   
5. Je vier Prints `CON_10pol_PIN_V2` im Segment 2 und 3 stellen die Ein- und Ausgangspins der 10-poligen Schaltblock-Ausg&auml;nge f&uuml;r die I²C-Verdrahtung zur Verf&uuml;gung.   
6. Im Segment 2 und 3 sind je zwei PCF 8574-I/O-Prints montiert (einer f&uuml;r die Ausgangs- und einer f&uuml;r die Eingangssignale).   
7. Der Anschluss der Weichen und des Entkupplers erfolgt an Prints 3x `CON_6pol_3_V1` bzw. 1x `CON_6pol_6_V1` (f&uuml;r Dreiwegweiche).   

## 3.5 Gleisbau
### Anbringen der Stromversorgung am Gleis   
Zur Stromversorgung kann man Fleischmann 22217 Anschlu&szlig;kabel 2pol. Spur N verwenden oder man l&ouml;tet selbst Dr&auml;hte an die Gleisverbinder. Dies geht f&uuml;r Fleischmann-Schotterbett-Gleise sehr gut, w&auml;hrend die Verbinder von Gleisen ohne Schotterbett praktisch nicht l&ouml;tbar sind.   
Als Anschlussdraht verwendet man einen ca. 30 cm langen braunen Volldraht mit 0,32 mm² (22awg) f&uuml;r die n&ouml;rdliche Schiene und einen roten Draht f&uuml;r die s&uuml;dliche Schiene. Der Draht wird beidseitig ca. 6 mm abisoliert und f&uuml;r den Gleisverbinder-Anschluss hakenf&ouml;rmig gebogen, mit einer kleinen Zange etwas flachgedr&uuml;ckt und verzinnt.   
Dazu fixiert man am besten das Gleis mit einem Klebestreifen, schneidet mit einem Stanley-Messer die kleine Verbindung &uuml;ber dem Gleisverbinder heraus (damit man leichter l&ouml;ten kann ;) ), und verzinnt den Gleisverbinder. Im Bild unten sieht man rechts unten die kleine Plastikverbindung &uuml;ber dem Gleisverbinder, der rechts oben entfernt ist.   

Loeten_Gleisanschluss1   
_Bild 32: Vorbereitung des Anl&ouml;tens einer Stromzuf&uuml;hrung._   

### Gleise aufkleben   
#### Vorbereitung der Weichen   
Um den Antrieb als Unterflurantrieb zu verwenden, muss man den Schalthebel der Weiche herausziehen und um 180° gedreht wieder einstecken. Danach kann der Antrieb mit der Oberseite nach unten aufgesteckt werden.   
#### Vorbereitung Stromzuf&uuml;hrung   
Verwendet man die Stromzuf&uuml;hrungskabel Fleischmann 22217, so muss man immer oberhalb der Kontaktstelle eine Bohrung setzen (4 mm), um die Kabel nach unten durchf&uuml;hren zu k&ouml;nnen.   
Bei selbst gel&ouml;teten Stromzuf&uuml;hrungen muss jeweils direkt unter jedem Gleisverbinder eine Bohrung gesetzt werden.   
#### Vorbereitung Entkupplungsgleis   
F&uuml;r den Antrieb des Entkupplungsgleises 9112 (oder 22212) muss ebenfalls eine 4 mm-Bohrung gesetzt werden.   
#### Gleise aufkleben   
Alle Kabel in die Bohrungen einf&auml;deln und nach unten ziehen, bis die Gleise etwa 5 bis 10 cm Abstand zur zuk&uuml;nftigen Position haben. Die Grundplatte etwas schr&auml;g stellen, damit die Kabel nicht geknickt werden.   
Alle Bereiche markieren, auf die kein Leim aufgetragen werden darf (oder mit Klebeband abdecken):   
* Weichenantrieb   
* Entkupplungsgleis   
* Ausgleichsgleise am linken und rechten Rand (Ost und West)   

Das Gleisbett mit Leim versehen. Dabei ist zu beachten, dass im Bereich der Weiche und des Entkupplungsgleises m&ouml;glichst wenig Leim (oder gar kein Leim) aufgebracht wird, damit kein Leim in die Antriebe gelangt und diese verklebt!   
Da die Ausgleichsgleise zur Anpassung von Abst&auml;nden an den Modulgrenzen dienen, darf in diesem Bereich ebenfalls KEIN Leim aufgebracht werden!   
Danach die Gleise fertig zusammenstecken und vorsichtig an den Kabeln ziehen, bis die Gleise auf dem Leim liegen.   
Da die beiden Ausgleichsgleise am linken und rechten Rand im Betrieb mechanisch in L&auml;ngsrichtung beansprucht werden, sollten sie mit je einem Gleisnagel zus&auml;tzlich fixiert werden. Dabei muss der Gleisnagel an der vom Rand entfernten Gleisseite eingeschlagen werden.   

Das Modul mit eingesetzter Grundplatte und Gleisen sieht folgenderma&szlig;en aus:   
Montiertes Gleis   
_Bild 33: Rahmen mit Grundplatte und Gleisen._   

[Zum Seitenanfang](#up)   

# 4. Elektrische Verdrahtung des Moduls   
## 4.1 Verdrahrungsplan
Das folgende Bild gibt eine &Uuml;bersicht &uuml;ber die Verdrahtung der verwendeten Komponenten:   
&Uuml;bersicht M12   
_Bild 34: &Uuml;bersichtsplan Modul 12_   

## Bedeutung der einzelnen Komponenten
Die folgende Aufz&auml;hlung enth&auml;lt Links zu Beschreibungen und zum Bau der Komponenten.   

`SUB25_10 ....` [Modul-Verbinder mit Netzteil](/fab/rcc1_supply/LIESMICH.md#x30)      
`uC_OLED .....` [Block OLED-Fassung mit I²C- und DCC-Shield sowie ESP32](/fab/rcc2_esp32/LIESMICH.md#x15)   

-------   

`1OUT ........` [Block zur Ausgabe der Wechselspannung](/fab/rcc4_block/LIESMICH.md#x40) zB f&uuml;r Entkuppler   
`2IO..........` [Block zum Schalten eines abschaltbaren Gleises](/fab/rcc4_block/LIESMICH.md#x50)   
`W2 ..........` [Block zum Schalten einer (Zweiweg-)Weiche](/fab/rcc4_block/LIESMICH.md#x20)   
`W3 ..........` [Block zum Schalten einer Dreiwegweiche](/fab/rcc4_block/LIESMICH.md#x30)   

-------   

`10pol_PIN....` Umsetzer vom 10-poligen Flachbandkabel auf 2x4 Pin [als &auml;ltere Version `CON_10pol_PIN`](/fab/rcc5_add_ons/LIESMICH.md#x90) bzw. [als neuere Version `CON_10pol_2x4`](/fab/rcc5_add_ons/LIESMICH.md#x80)   
`CON_6pol-3 ..` [Umsetzer vom 6-poligen Flachbandkabel auf 3 Pins](/fab/rcc5_add_ons/LIESMICH.md#x40) zum Beispiel f&uuml;r eine Zweiwegweiche _W2_ oder einen Entkuppler _1OUT_   
`CON_6pol-6 ..` [Umsetzer vom 6-poligen Flachbandkabel auf 6 Pins](/fab/rcc5_add_ons/LIESMICH.md#x50) zum Beispiel f&uuml;r eine Dreiwegweiche _W3_    
`CON_1xIO ....` [Umsetzer vom 6-poligen Flachbandkabel auf Schraubklemmen](/fab/rcc5_add_ons/LIESMICH.md#x60) zum einfachen Anschluss des Fahrstromschalters _2IO_.   
`CON_2xIO ....` [Zweifach-Umsetzer vom 6-poligen Flachbandkabel auf Schraubklemmen](/fab/rcc5_add_ons/LIESMICH.md#x70) zum einfachen Anschluss zweier Fahrstromschalter _2IO_.   

-------   

`i2c_20mm ....` [I²C-Halterung 20 mm](/fab/rcc3_i2c/LIESMICH.md#x20)   
`PCF8574 .....` [I²C-PCF8574-I/O-Platinen](/fab/rcc3_i2c/LIESMICH.md)   
`i2c_Term ....` [I²C-Halterung mit Abschluss-Widerst&auml;nden](/fab/rcc3_i2c/LIESMICH.md#x60)   

Da Entkuppler beim Schalten St&ouml;rspannungen erzeugen, werden direkt beim Entkuppleranschluss (CON_6pol-3) und am Ende des 6-poligen Stromversorgungskabels (an den Wechselstromklemmen Pin 4 und Pin 6) 100nF-Kondensatoren angebracht.   

## 4.2 Verdrahtung der Stromversorgung und des Fahrstroms
1. Verbinden des Anschlusses "POWER" der Versorgungsplatine `RW_5V_SUB25_10` mit den acht Schaltbl&ouml;cken mit einem 6-poligen, ca. einen Meter langen Flachbandkabel und 10 montierten Pfostenverbindern. Der erste Pfostenverbinder dient zum Anschluss an die Versorgungsplatine, der Pfostenverbinder am Ende der Leitung dient einem eventuell erforderlichem Verl&auml;ngern des Flachbandkabels bzw. zum Anschluss von 100 nF-Kondensatoren zwischen V+ und V- sowie 5V und 0V. (Der Stecker ist im _Bild 24_ rechts oben noch nicht angebracht...)   
Abschlusskondensatoren   
_Bild 35: Abschlusskondensatoren am Ende des POWER-Kabels_   

2. Verbinden aller Fahrstromanschl&uuml;sse mit den entsprechenden Klemmen.   
3. Verbinden des Fahrstroms (NN, SS) von der Versorgungsplatine `RW_5V_SUB25_10` zu den Platinen `CON_2pol_141`, `CON_1xIO`, `CON_2xIO` sowie den L&uuml;sterklemmen GW (Gleis West) und GO (Gleis Ost).   
4. Verbinden der Anschl&uuml;sse der beiden Weichenantriebe der Dreiwegweiche mit der Platine `CON_6pol_6` (linke Weiche = Antrieb n&auml;her zu den Schaltbl&ouml;cken = Pin 1 und 3, Masse an Pin 2).   
5. Verbinden der Anschl&uuml;sse der beiden Zweiweg-Weichenantriebe mit den Platinen `CON_6pol_3` (Masse = schwarzes Kabel an Pin 2).   
6. Verbinden der Anschl&uuml;sse des Entkupplers mit der Platine `CON_6pol_3`.   
_Wichtig_: Da der Entkuppler St&ouml;rspannungen erzeugt, muss ein 100 nF-Kondensator parallel zu den Klemmen V+ und V- geschaltet werden.   
Entst&ouml;rkondensator   
_Bild 36: Entst&ouml;rkondensator am Entkuppler_   

Die Verdrahtung der Stromversorgung im &Uuml;berblick:   

Verdrahtung 1   
_Bild 37: Verdrahtung Stromversorgung_   

### Erster Test der Verdrahtung   
Mit der bisherigen Verdrahtung ist es bereits m&ouml;glich, einen h&auml;ndischen Betrieb durchzuf&uuml;hren. Dabei kann vor allem der richtige Anschluss der Weichen und die Funktion aller Stromzuf&uuml;hrungen (L&ouml;tstellen) getestet werden.   
1. Anstecken eines 25-poligen Steckers mit Fahrstrom- und Wechselstromversorgung: Die LEDs der Schaltbl&ouml;cke sollten leuchten.   
2. Test der Ansteuerung der Dreiwegweiche Links-Mitte und Mitte-Rechts. Falls ein Fehler auftritt: Anschl&uuml;sse 1 und 3 vertauschen.   
2. Test der Ansteuerung der Zweiwegweichen. Stimmt die Anzeige-LED f&uuml;r Gerade und Abzweig? Schaltet die Weiche entsprechend dem Taster auf "Gerade" oder "Abzweig"? Falls nicht: Anschl&uuml;sse 1 und 3 vertauschen.   
3. Arbeitet der Entkuppler?   
4. Stimmen alle LED-Anzeigen mit der entsprechenden Hardware &uuml;berein?   
5. Fahrstrom Gleis 1, 2, 3 und 1A mit den gr&uuml;nen Tastern einschalten, Probefahrt mit einer Lokomotive &uuml;ber alle Gleise.   

## 4.3 Vorbereitung Mikrocontroller
1. Verbinden des Anschlusses "DCC" der Versorgungsplatine `RW_5V_SUB25_10` mit dem Mikrocontroller &uuml;ber ein ca. 30 cm langes, 6-poliges Kabel.   
2. Verbinden des Mikrocontrollers mit den I²C-PCF8574-I/O-Expanderplatinen mit 20 cm langen, 4-poligen Kabeln mit male-female-Steckern.   
3. Programmierung des Mikrocontrollers mit der Software `rcc_module12_V1`.   

## 4.4 Verdrahtung I²C-Bus
1. Verbinden der acht 10-poligen Stecker der Schaltbl&ouml;cke mit den 10-poligen Steckern der Platinen `CON_10pol_PIN`.   

2. Herstellung der Verbindungen zwischen den Stiftleisten der `CON_10pol_PIN`-Platinen und den I²C-PCF8574-I/O-Expanderplatinen mit 10 cm langen Leitungen female-female.    

Im Segment 2:   
   * I/O-Expander 0x20 - Pin 0 ` -->--braun---> ` Block DCC 129, Pin 1 - IN   
   * I/O-Expander 0x20 - Pin 1 ` -->--rot-----> ` Block DCC 121/122, Pin 1 - IN   
   * I/O-Expander 0x20 - Pin 2 ` -->--orange--> ` Block DCC 121/122, Pin 2 - IN   
   * I/O-Expander 0x20 - Pin 3 ` -->--gelb----> ` Block DCC 121/122, Pin 3 - IN   
   * I/O-Expander 0x20 - Pin 4 ` -->--gruen---> ` Block DCC 123, Pin 1 - IN   
   * I/O-Expander 0x20 - Pin 5 ` -->--blau----> ` Block DCC 123, Pin 2 - IN   
   * I/O-Expander 0x20 - Pin 6 ` -->--violett-> ` Block DCC 124, Pin 1 - IN   
   -------   
   * I/O-Expander 0x21 - Pin 0 ` <--braun---<-- ` Block DCC 129, Pin 1 - OUT   
   * I/O-Expander 0x21 - Pin 1 ` <--rot-----<-- ` Block DCC 121/122, Pin 1 - OUT   
   * I/O-Expander 0x21 - Pin 2 ` <--orange--<-- ` Block DCC 121/122, Pin 2 - OUT   
   * I/O-Expander 0x21 - Pin 3 ` <--gelb----<-- ` Block DCC 121/122, Pin 3 - OUT   
   * I/O-Expander 0x21 - Pin 4 ` <--gruen---<-- ` Block DCC 123, Pin 1 - OUT   
   * I/O-Expander 0x21 - Pin 5 ` <--blau----<-- ` Block DCC 123, Pin 2 - OUT   
   * I/O-Expander 0x21 - Pin 6 ` <--violett-<-- ` Block DCC 124, Pin 1 - OUT   

Im Segment 3:   
   * I/O-Expander 0x22 - Pin 0 ` -->--braun---> ` Block DCC 128, Pin 1 - IN   
   * I/O-Expander 0x22 - Pin 1 ` -->--rot-----> ` Block DCC 128, Pin 2 - IN   
   * I/O-Expander 0x22 - Pin 2 ` -->--orange--> ` Block DCC 127, Pin 1 - IN   
   * I/O-Expander 0x22 - Pin 3 ` -->--gelb----> ` Block DCC 126, Pin 1 - IN   
   * I/O-Expander 0x22 - Pin 4 ` -->--gruen---> ` Block DCC 125, Pin 1 - IN   
   -------   
   * I/O-Expander 0x23 - Pin 0 ` <--braun---<-- ` Block DCC 128, Pin 1 - OUT   
   * I/O-Expander 0x23 - Pin 1 ` <--rot-----<-- ` Block DCC 128, Pin 2 - OUT   
   * I/O-Expander 0x23 - Pin 2 ` <--orange--<-- ` Block DCC 127, Pin 1 - OUT   
   * I/O-Expander 0x23 - Pin 3 ` <--gelb----<-- ` Block DCC 126, Pin 1 - OUT   
   * I/O-Expander 0x23 - Pin 4 ` <--gruen---<-- ` Block DCC 125, Pin 1 - OUT   

## 4.4 Modulverbindung
Damit Module aneinandergereiht werden k&ouml;nnen m&uuml;ssen noch die 10 Schraubklemmen bei den 25-poligen Steckern miteinander verbunden werden.   
Nach NEM908D erfolgt dies so, dass die Leitungen elektrisch ausgekreuzt, aber physikalisch gerade durchverbunden werden. Das bedeutet, dass sich zB der Fahrstrom des Gleises NN auf dem West-Stecker auf dem Pin 1 und auf dem Ost-Stecker auf dem Pin 13 befindet!   
Wiring_NEM908D   
_Bild 38: 25polige Sub-D Stecker auf dem Modul mit Pin-Belegung_   

[Siehe auch `/info/con_NEM908/LIESMICH.md`](/info/con_NEM908/LIESMICH.md)   

F&uuml;r die Verbindung der Pins kann zB 10-poliges Kabel verwendet werden.   

Stecker West   
_Bild 39: Verdrahtung Stecker West_   

Stecker Ost   
_Bild 40: Verdrahtung Stecker Ost_   

[Zum Seitenanfang](#up)   

# 5. Steuerungssoftware   
## 5.1 Anpassung des Demoprogramms f&uuml;r Modul 12
1. Erstellen eines neuen Verzeichnisses mit dem Namen `rcc_module12_V1`.   
2. Kopieren der Dateien aus dem Verzeichnis `rcc_demo1` in das neue Verzeichnis `rcc_module12_V1`.   
3. L&ouml;schen der *.md-Dateien im Verzeichnis `rcc_module12_V1`.   
4. Umbenennen der Dateien `rcc_demo1.cpp` und `rcc_demo1_text.h` in `rcc_module12_V1.cpp` und `rcc_module12_text.h` im Verzeichnis `rcc_module12_V1/src`.   
5. Starten von Visual Studio Code und &Ouml;ffnen des Ordners (Verzeichnisses) `software/rcc_module12_V1`.   
6. Umbenennen von `rcc_demo1` in `rcc_module12` __*in allen Dateien*__ (Men&uuml;punkt Bearbeiten - In Dateien ersetzen).   
7. Datei `rcc_module12_V1.cpp` im Editorfenster &ouml;ffnen.   
8. Umbenennen von `DEBUG_99` in `DEBUG_12` __*in allen Dateien*__ (Men&uuml;punkt Bearbeiten - In Dateien ersetzen).   
9. Umbenennen von `VERSION_99` in `VERSION_12` __*in allen Dateien*__ (Men&uuml;punkt Bearbeiten - In Dateien ersetzen).   
10. Anpassen des Starttextes in der Datei `rcc_module12_text.h`:   
```  
#define  INFOLINES_NUM     20
  #define  INFOLINES { \
   "Modul 12:            ", \
   "Ausweichstelle und   ", \
   "Abstellgleis         ", \
   VERSION_99_1, \
   " Weiter: Taste IO19  ", \
   \
   "DCC-Adressen      1/3", \
   "121 3-Wegweiche Links", \
   "122 3-Wegweiche Recht", \
   "123 Weiche Gleis 1A  ", \
   " Weiter: Taste IO19  ", \
   \
   "DCC-Adressen      2/3", \
   "124 Entkuppler Gleis3", \
   "125 Fahrstrom Gleis 1", \
   "126 Fahrstrom Gleis 2", \
   " Weiter: Taste IO19  ", \
   \
   "DCC-Adressen      3/3", \
   "127 Fahrstrom Gleis 3", \
   "128 Weiche W2 Ost   ", \
   "129 Fahrstrom Gleis1A", \
   " Weiter: Taste IO19  " \
   }
```  
und im englischsprachigen Abschnitt   
```   
#define  INFOLINES_NUM     20
  #define  INFOLINES { \
   "Module 12:           ", \
   "passing siding and   ", \
   "siding               ", \
   VERSION_99_1, \
   " Next: Button IO19   ", \
   \
   "DCC-Addresses     1/3", \
   "121 3way-Turnout left", \
   "122 3way-Turnout righ", \
   "123 Turnout Track 1A ", \
   " Next: Button IO19   ", \
   \
   "DCC-Addresses     2/3", \
   "124 Uncoupler Track 3", \
   "125 Current Track 1  ", \
   "126 Current Track 2  ", \
   " Next: Button IO19   ", \
   \
   "DCC-Addresses     3/3", \
   "127 Current Track 3  ", \
   "128 Turnout W2 East  ", \
   "129 Current Track 1A ", \
   " Next: Button IO19   ", \
   }
```   
11. Anpassen der projektspezifischen Daten in der Datei `dcc_config.h`. Details dazu [siehe /software/rcc_demo1/CUSTOMIZE_D.md](/software/rcc_demo1/CUSTOMIZE_D.md). Insbesondere:   

_Zeile 17 und 18_:   
```   
#define  VERSION_99     "2025-02-05 rcc_module12_V1"
#define  VERSION_99_1   "Version 2025-02-05"
```   
_Zeile 27_:   
```   
#define  TOPIC_BASE     "rcc/module12"
```   
_Zeile 34_:   
```   
#define  SCREEN_TITLE   "RCC Module 12"
```   
_Ab Zeile 78:_   
```   
//-------disconnectable track (Fahrstrom)-----------------------
#define  RCOMP_1        RC_TYPE_DT,"G1A", 129, EX0,PIN0,NO_PIN, EX1,PIN0,NO_PIN, 0,0
//-------three way turnout (Dreiwegweiche)----------------------
// A=0: curved, B=0: stright (@ 3 pin: middle pin=0V -> stright)
#define  RCOMP_2L       RC_TYPE_T3,"TWL",121, EX0,PIN1,PIN2,   EX1,PIN1,PIN2, 500,0
#define  RCOMP_2R       RC_TYPE_T3,"TWR",122, EX0,PIN3,PIN2,   EX1,PIN3,PIN2, 500,0
// ------two way turnout (Zweiwegweiche = Standardweiche)-------
// Two expander pins A B to control 2way turnout (active low!)
// A=0: curved, B=0: stright
#define  RCOMP_3        RC_TYPE_TO,"T1", 123, EX0,PIN4,PIN5,   EX1,PIN4,PIN5, 500,0
// ------uncoupler (Entkuppler)---------------------------------
#define  RCOMP_4        RC_TYPE_UC,"E1", 124, EX0,PIN6,NO_PIN, EX1,PIN6,NO_PIN, 1500,0

//-------disconnectable track (Fahrstrom)-----------------------
#define  RCOMP_5        RC_TYPE_DT,"G1", 125, EX2,PIN4,NO_PIN, EX3,PIN4,NO_PIN, 0,0
//-------disconnectable track (Fahrstrom)-----------------------
#define  RCOMP_6        RC_TYPE_DT,"G2", 126, EX2,PIN3,NO_PIN, EX3,PIN3,NO_PIN, 0,0
//-------disconnectable track (Fahrstrom)-----------------------
#define  RCOMP_7        RC_TYPE_DT,"G3", 127, EX2,PIN2,NO_PIN, EX3,PIN2,NO_PIN, 0,0
// ------two way turnout (Zweiwegweiche = Standardweiche)-------
// Two expander pins A B to control 2way turnout (active low!)
// A=0: curved, B=0: stright
#define  RCOMP_8        RC_TYPE_TO,"T2", 128, EX2,PIN0,PIN1,   EX3,PIN0,PIN1, 500,0

//.......Array of all railway components........................
#define  RCOMP_NUM      9
strRcomp aRcomp[RCOMP_NUM] = {
 {RCOMP_1},{RCOMP_2L},{RCOMP_2R},{RCOMP_3},{RCOMP_4},{RCOMP_5},{RCOMP_6},{RCOMP_7},{RCOMP_8}
};
```   

12. Anpassen des Kommentars am Beginn der Datei `rcc_module12_V1.cpp`, zB.   
```   
//_____rcc_module12_V1___________________________khartinger_____
// This program for an ESP32 is used for the self-built 
// model railroad switching blocks of module 12.
// ...
```   

## 5.2 Programmierung des Mikrocontrollers
Zum Programmieren des Mikrocontrollers wird das Modul von der Stromversorgung getrennt und der Mikrocontroller &uuml;ber das USB-Kabel mit dem Programmierger&auml;t (PC oder Laptop) verbunden.   
Danach wird Visual Studio Code mit installiertem PlatformIO gestartet und der Mikrocontroller mit der Software `rcc_module12_V1` programmiert.   

[Zum Seitenanfang](#up)   

# 6. Probebetrieb
## 6.1 Modul-Start
1. MQTT-Server starten.   
2. Einen Laptop oder PC mit dem Netzwerk des MQTT-Servers verbinden und die Software `mosquitto_sub` in einem Kommando-Fenster mit diesem Kommando starten:   
   `mosquitto_sub -h 10.1.1.1 -t rcc/# -v`   
3. Anstecken eines 25-poligen Steckers mit Fahrstrom- und Wechselstromversorgung: Die LEDs der Schaltbl&ouml;cke sollten entspechend der Hardware-Stellung richtig leuchten.   
4. Die Info-Seiten auf dem OLED mit dem neben liegenden Taster weiterschalten. Wenn alles funktioniert, erscheint auf dem OLED-Display folgende Anzeige:   
```   
  RCC Module 12     
MQTT OK    Raspi11  
rcc/module12        
G1A TWL TWR T1  E1  
Aus __  __  _/  Aus 
129 121 122 123 124 
```   

Die Anzeige der Stellung der Weichen 121 bis 123 ist abh&auml;ngig von der tats&auml;chlichen Stellung der Weichen. Die Anzeige wechselt alle 5 Sekunden weiter.   

5. Im Kommandofenster am Laptop erscheint die Startmeldung des Moduls:   
`rcc/start/mqtt {"topicbase":"rcc/module12"}`   

## 6.2 Test mit MQTT
Ein zweites Kommando-Fenster am Laptop &ouml;ffnen und folgendes eingeben:   
`mosquitto_pub -h 10.1.1.1 -t rcc/module12/get -m ?`   
Im ersten Kommando-Fenster werden die m&ouml;glichen Befehle angezeigt:   
```   
rcc/module12/get ?
rcc/module12/ret/?
get: ?|help|version|ip|topicbase|eeprom|byname|bydcc|G1A|129|TWL|121|TWR|122|T1|123|E1|124|G1|125|G2|126|G3|127|T2|128|
set: topicbase|eeprom0|G1A|129|TWL|121|TWR|122|T1|123|E1|124|G1|125|G2|126|G3|127|T2|128|
sub:
pub:
MQTT: ../set/w1 -m 1|g|G OR -m 0|A|a|B|b (set by name)
      ../set/11 -m 1|g|G OR -m 0|A|a|B|b (set by dcc address)
      ../get -m byname|bydcc (values of all components)
```   

### Beispiele f&uuml;r Schaltbefehle  
Schalten der Weiche DCC 123 auf Gerade:   
`mosquitto_pub -h 10.1.1.1 -t rcc/module12/set/123 -m 1`   

Schalten der Weiche DCC 123 mit Namen T1 auf Abzweig (Bogen):   
`mosquitto_pub -h 10.1.1.1 -t rcc/module12/set/T1 -m 0`   

Einschalten des Fahrstroms im Gleis 2 (Durchfahrsgleis, DCC-Adresse 126):   
`mosquitto_pub -h 10.1.1.1 -t rcc/module12/set/126 -m 1`   
Die Anzeige geht von "Aus" (LED rot) auf "Ein" (LED gr&uuml;n), sofern nicht einer der beiden Taster gedr&uuml;ckt ist.   

Einschalten des Entkupplers (DCC 124):   
`mosquitto_pub -h 10.1.1.1 -t rcc/module12/set/124 -m 1`   
Der Entkuppler wird f&uuml;r 1,5 Sekunden eingeschaltet.   

## 6.3 Test mit DCC
Je nach DCC-Eingabeger&auml;t k&ouml;nnen die gleichen Aktionen wie mit MQTT durchgef&uuml;hrt werden.   
### Beispiel Roco Multi-Maus
* Weichensteuerung w&auml;hlen (Taste Lok/Weiche) Taste_Lok_Weiche   
* DCC-Adresse 123 eingeben Anzeige_W0123   
* Mit den Pfeiltasten die Weiche schalten Pfeiltasten   

[Zum Seitenanfang](#up)   

# 7. Abschlie&szlig;ende Arbeiten   
## 7.1 Weichenabdeckungen   
F&uuml;r die Montage der Unterflur-Weichenantriebe muss die Grundplatte ausgeschnitten werden (siehe Bild 26 und Bild 27). F&uuml;r die Landschaftsgestaltung m&uuml;ssen diese Ausschnitte jedoch gut abgedeckt werden, damit keine Schotterk&ouml;rner etc. in die Weichenantriebe gelangen. Auf dem Modul M12 werden zwei verschiedene Arten von Abdeckungen ben&ouml;tigt:   
* Drei flache Abdeckungen (ausgehend von Ebene E8)   
* Eine hohe Abdeckung f&uuml;r den rechten Antrieb der Dreiweg-Weiche (d.h. ausgehend von der Grundplatte E0)   

Bei den flachen Abdeckungen reichen die Weichenantriebe 1,5 mm &uuml;ber das Niveau E8 (Schaumstoff-Obergrenze):   
* 0,5 mm Metallplatte auf der Weichenunterseite + 0,5 mm Metall-Haltenasen + 0,5 mm H&ouml;henausgleich, falls die Weiche Oberflur montiert wird...   
Zum Abdecken des Ausschnitts kann daher eine 0,5 mm Kunststoff-Folie als Basisabdeckung sowie eine 1 mm Folie dar&uuml;ber + eine 0,5 mm Folie &uuml;ber dem Antrieb verwendet werden.   
Als Alternative ist auch 3D-gedruckte Abdeckungen m&ouml;glich, wie sie im _Bild 33_ zu sehen sind.   
3D Weichenabdeckung   
_Bild 41: 3D-Druck-Abdeckungen der Weichenaussparungen_   

Die St&auml;rke der Abdeckungen betr&auml;gt 0,6 mm (= 3 Schichten), die Befestigung erfolgt mit Gleisn&auml;geln (0,7 mm Durchmesser). Die mittlere Abdeckung wurde mit einer Schere passend geschnitten.   

## 7.2 Bodenabdeckung   
Um die Verkabelung zu sch&uuml;tzen, kann man auch Teile des Bodens mit durchsichtigen Folien (zB mit 1 mm St&auml;rke) abdecken.   

## 7.3 Modell-Hintergrundbild   
Das Modellhintergrundbild sollte bei 25 cm Modultiefe zumindest 15,5 cm hoch sein.   

[Zum Seitenanfang](#up)

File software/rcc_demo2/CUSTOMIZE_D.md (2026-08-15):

<table><tr><td></td><td>
Letzte &Auml;nderung: 4.1.2026 <br>   
<h1>Anpassen des Demo-Programms an eigene Bed&uuml;rfnisse</h1>
<a href="/software/rcc_demo2/CUSTOMIZE_E.md">==> English version</a>&nbsp; &nbsp; &nbsp; 
</td></tr></table>   

# Einleitung
F&uuml;r viele Eins&auml;tze des RCC-Systems reicht es, in der [Konfigurationsdatei `src/dcc_config.h`](#x20) die verwendeten Komponenten und ihre Verdrahtung anzugeben sowie den Text der Informationsseiten beim Programmstart in der [Datei `src/rcc_demo2.text.h`](#x30) anzupassen.   
Das Steuerprogramm `rcc_demo2.cpp` muss im Normalfall nicht ver&auml;ndert werden. Falls man die Steuerung erweitern m&ouml;chte, so findet man eine detaillierte Beschreibung der Demo-Software unter [/software/rcc_demo2/DETAILS_D.md](/software/rcc_demo2/DETAILS_D.md).   

# Die Konfigurationsdatei dcc_config.h
## &Uuml;bersicht
In der Konfigurationsdatei `dcc_config.h` werden alle wesentlichen Projekteigenschaften definiert wie   
* Versionsbezeichnung des Programms (zB das Datum der letzten &Auml;nderung)   
* Informationen zum verwendeten Netzwerk (WLAN)   
* implementierte MQTT GET- und SET-Nachrichten   
* Eigenschaften des verwendeten Displays   
* ein m&ouml;glicher Offset f&uuml;r DCC-Adressen   
* die Anzahl der I²C-I/O-Expander, ihre Namen, Adressen und Startwerte   
* die Anzahl der Eisenbahnkomponenten und deren Typ, Name, DCC-Adresse, Expander-Nummer und -Pinbelegung sowie Schaltzeiten   

## Beispiel Demo-Programm "dcc_demo2"   
Speziell die elektrische Verdrahtung der Komponenten muss bekannt sein und in der Konfigurationsdatei abgebildet werden. F&uuml;r das Demo-Programm `dcc_demo2` wird von folgender Verdrahtung ausgegangen:   
* 2x I²C-Expander mit den Namen `pcf8574_out` (7-Bit-Adresse 0x20) und `pcf8574_in` (7-Bit-Adresse 0x21)., d.h. je ein Expanderboard f&uuml;r Ausg&auml;nge und ein Expanderboard f&uuml;r Eing&auml;nge   
* 1x Entkuppler (Name "UC", DCC-Adresse 11) an Pin 0 der I²C-Expander   
* 1x Zweiwegweiche (Name "T2", DCC-Adresse 21) an Pin 1 und 2 der I²C-Expander   
* 1x Dreiwegweiche (zwei Antriebe mit den Namen "T3L" und "T3R", DCC-Adresse 31 und 32) an Pin 3, 4 und 5 der I²C-Expander   
* 1x Fahrstromschalter (Name "DT", DCC-Adresse 41) an Pin 6 der I²C-Expander   
* 1x Blinklicht (Name "BL", DCC-Adresse 51) an Pin 7 der I²C-Expander   

Das folgende _Bild 1_ veranschaulicht nochmals diese Daten.   

circuit_rcc_demo2   
_Bild 1: Verdrahtung des Beispiels `rcc_demo2`_   

Das Listing zeigt die Konfigurationsdatei f&uuml;r das Demo-Programm __mit Zeilennummern__. Danach wird erkl&auml;rt, welche Zeilen angepasst werden m&uuml;ssen.   

```   
1	//_____dcc_config.h______________________________khartinger_____
2	// Configure file for ESP32 railroad DCC decoder program
3	// rcc_demo2
4	//
5	// Created by Karl Hartinger, November 14, 2024
6	// Changes:
7	// 2024-11-28 Change program name
8	// 2025-01-03 Change TOPIC_BASE
9	// 2025-06-18 Add "signal"
10	// 2026-01-04 Add RC_TYPE_TX, RC_TYPE_DD
11	// Released into the public domain.
12	
13	#ifndef DCC_CONFIG_H
14	 #define DCC_CONFIG_H
15	 #include <Arduino.h>                  // String, int32_t
16	 #include "src/pcf8574/D1_class_PCF8574.h"
17	
18	//_______program version________________________________________
19	#define  VERSION_99     "2026-01-04 rcc_demo2"
20	#define  VERSION_99_1   "Version 2026-01-04"
21	
22	#define  SHOW_INFOPAGE_SEC  20             // time to show one page
23	
24	//_______Network and MQTT data__________________________________
25	#define  _USE_WIFI_     true
26	#define  _SSID_         "Raspi11"
27	#define  _PASS_         "12345678"
28	#define  _HOST_         "10.1.1.1"
29	#define  TOPIC_BASE     "rcc/demo1"
30	#define  TOPIC_GET      "?,help,version,ip,signal,topicbase,eeprom,byname,bydcc,status"
31	#define  TOPIC_SET      "topicbase,eeprom0"
32	#define  TOPIC_SUB      ""
33	#define  TOPIC_PUB      ""
34	
35	//_______1.54" display data (SSD1309, 128x64 pixel, I2C)________
36	#define  SCREEN_TITLE   "RCC_Demo1"
37	#define  SCREEN_LINE_MAX 6
38	#define  SCREEN_LINE_LEN 21
39	
40	//_______DCCex__________________________________________________
41	#define  DCC_OFFSET     4
42	
43	//_______Hardware: IO expander PCF8574__________________________
44	#define  IOEX_NUM       2              // number of IO expander
45	PCF8574  pcf8574_out(1,0x20,0xFF);     // 8 digital OUT
46	PCF8574  pcf8574_in (1,0x21,0xFF);     // 8 digital IN
47	PCF8574 *pIOEx[IOEX_NUM]={&pcf8574_out, &pcf8574_in}; // IO expander
48	
49	//_______Definitions for railroad components____________________
50	//.......values for every railroad component....................
51	// e.g. turnout, uncoupler, disconnectable track, ...
52	#define  NO_PIN         -1   // no pin @ PCF8574 (0...7)
53	#define  RC_TYPE_UC     1    // uncoupler (Entkuppler)
54	#define  RC_TYPE_TO     2    // turnout (Weiche)
55	#define  RC_TYPE_T3     3    // 3way turnout (Dreiwegweiche)
56	#define  RC_TYPE_DT     4    // disconnectable track (Fahrstrom)
57	#define  RC_TYPE_TX     5    // double slip turnout/switch (Doppelkreuzungsweiche)
58	#define  RC_TYPE_DD     6    // double pole, double throw (2x UM)
59	#define  RC_TYPE_BL     9    // blink light (Blinklicht)
60	
61	//.......All properties of a railroad component.................
62	struct strRcomp {
63	  int    type;          // RC_TYPE_TO, RC_TYPE_UC, RC_TYPE_DT
64	  String name;          // short name like T1, U1, D1, W1, E1...
65	  int    dcc;           // dcc address of the component
66	  int    outPCF;        // aIOEx index of PCF8574 output device
67	  int    outBitA;       // bit PCF8574 for turnout straight (Gerade)
68	  int    outBitB;       // bit PCF8574 for turnout curved (Abzweig)
69	  int    inPCF;         // aIOEx index of PCF8574 input device
70	  int    inBitA;        // bit number at PCF8574 input straight=1
71	  int    inBitB;        // bit number at PCF8574 input curved=1
72	  int32_t msOn;         // ms on
73	  int32_t msOff;        // ms off
74	};
75	
76	//_______Railroad commands______________________________________
77	// railroad components:  type,name (max 3 char),dcc,
78	//                      pIOEx-out-index,outBitA,outBitB, 
79	//                      pIOEx-in-index inBitA inBitB
80	//                      msOn,msOff
81	// railroad component name max. 3 chars
82	// ------uncoupler (Entkuppler)---------------------------------
83	#define  RCOMP_1        RC_TYPE_UC,"UC", 11, EX0,PIN0,NO_PIN, EX1,PIN0,NO_PIN, 1500,0
84	// ------two way turnout (Zweiwegweiche = Standardweiche)-------
85	// Two expander pins A B to control 2way turnout (active low!)
86	// A=0: curved, B=0: straight
87	#define  RCOMP_2        RC_TYPE_TO,"T2", 21, EX0,PIN1,PIN2,   EX1,PIN1,PIN2, 500,0
88	//-------three way turnout (Dreiwegweiche)----------------------
89	// A=0: curved, B=0: straight (@ 3 pin: middle pin=0V -> straight)
90	#define  RCOMP_3L       RC_TYPE_T3,"T3L",31, EX0,PIN3,PIN4,   EX1,PIN3,PIN4, 500,0
91	#define  RCOMP_3R       RC_TYPE_T3,"T3R",32, EX0,PIN5,PIN4,   EX1,PIN5,PIN4, 500,0
92	//-------disconnectable track (Fahrstrom)-----------------------
93	#define  RCOMP_4        RC_TYPE_DT,"DT", 41, EX0,PIN6,NO_PIN, EX1,PIN6,NO_PIN, 0,0
94	//-------blink light (Blinklicht)-------------------------------
95	#define  RCOMP_5        RC_TYPE_BL,"BL", 51, EX0,PIN7,NO_PIN, EX1,NO_PIN,NO_PIN, 500,500
96	
97	//...if you want to test TX and/or DD: replace RCOMP_2/RCOMP_4..
98	//-------double slip turnout/switch (Doppelkreuzungsweiche)-----
99	//#define  RCOMP_2        RC_TYPE_TX,"TX", 21, EX0,PIN1,PIN2,   EX1,PIN1,PIN2, 500,0
100	//-------double pole, double throw (2x UM)----------------------
101	//#define  RCOMP_4        RC_TYPE_DD,"DD", 41, EX0,PIN6,NO_PIN, EX1,PIN6,NO_PIN, 0,0
102	
103	//.......Array of all railroad components........................
104	#define  RCOMP_NUM      6
105	strRcomp aRcomp[RCOMP_NUM] = {
106	 {RCOMP_1},{RCOMP_2},{RCOMP_3L},{RCOMP_3R},{RCOMP_4},{RCOMP_5}
107	};
108	#endif
```   

## Erforderliche Anpassungen in der Datei dcc_config.h
Die folgende Tabelle erkl&auml;rt die Bedeutung der einzelnen Zeilen in der Demo-Konfigurationsdatei `dcc_config.h`. Die Spalte `Chg` (change = &auml;ndern) gibt an, ob die Zeile(n) ge&auml;ndert werden sollen oder nicht:   
 1 = unbedingt &auml;ndern bzw. anpassen   
 2 = Zeile sollte angepasst werden   
 3 = Zeile kann ge&auml;ndert werden   
 x = Zeile(n) nicht &auml;ndern   

| Zeile | Chg | Bedeutung | 
|:---:|:---:|---|
| 19, 20  |  2  | Versionsnummer/&Auml;nderungsdatum der Datei. | 
| 22 |  3  | Anzahl Sekunden, wie lange jede Info-Seite beim Start angezeigt werden soll (zB 20 Sekunden). | 
| 25 |  2  | Soll ein Netzwerk (WLAN) verwendet werden? <br> true = ja, false = nein | 
| 26 - 28 |  2  | Wenn ein Netzwerk verwendet wird: Name und Passwort des WLAN sowie IP des Rechners, auf dem der MQTT-Broker l&auml;uft. | 
| 29 | __1__ | Das Basis-Topic, unter dem der Mikrocontroller MQTT-Nachrichten sendet oder empf&auml;ngt. | 
| 30 |  x  | Alle GET-Nachrichten, auf die der Mikrocontroller antwortet. | 
| 31 |  x  | Alle SET-Nachrichten, auf die der Mikrocontroller reagiert. | 
| 36 |  2  | Titel auf der OLED-Anzeige. | 
| 41 |  3  | Offset der DCC-Adressen, je nach DCC-Sendeger&auml;t (Wert kann 4 oder 0 sein). | 
| 44 | __1__ | Anzahl der eingesetzten I²C-I/O-Expander-Boards PCF8574 (2, 4, 6 oder 8). | 
| 45 - 46 |  2  | Je ein Objekt f&uuml;r jedes PCF8574-Board mit I²C-Busnummer (1), 7-Bit-I²C-Adresse (0x20, ...) und Startwert (meist 0xFF). | 
| 47 | __1__ | `*pIOEx[]` = Pointer-Array mit den Adressen der PCF8574-Board-Objekten (nicht auf das &-Zeichen vor den Namen vergessen!). | 
| 49 - 74 |  x  | Definitionen f&uuml;r die Eisenbahn-Komponenten. Sie befinden sich nur zum An- bzw. Nachschauen in dieser Datei. | 
| 76 - 101 | __1__ | Definition von Strukturen f&uuml;r jede einzelne Eisenbahn-Komponente. Der Aufbau jeder Zeile entspricht der Struktur von Zeile 58 bis 70. | 
| 104 | __1__ | Anzahl der Eisenbahn-Komponenten. | 
| 105 - 107 | __1__ | `aRcomp[]` = Array mit den Strukturen der einzelnen Eisenbahn-Komponenten. | 

# Die Textdatei dcc_demo2_text.h
Die Datei `dcc_demo2_text.h` enth&auml;lt Texte in deutscher und englischer Sprache f&uuml;r die OLED-Anzeige.   
Anzupassen sind die Texte, die sich in den Zeilen 42 bis 58 (Deutsch) und 80 bis 96 (Englisch) befinden. Dabei werden jeweils 5 Zeilen f&uuml;r 20 Sekunden (`SHOW_INFOPAGE_SEC`) angezeigt.   
Die Texte k&ouml;nnen auch gel&ouml;scht werden, dann ist die Konstante `INFOLINES_NUM` auf 0 zu setzen:   
```   
#define  INFOLINES_NUM     0
```   

[Zum Seitenanfang](#up)

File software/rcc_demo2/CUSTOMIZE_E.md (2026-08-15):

<table><tr><td></td><td>
Last modified: 2026-01-04 <br>   
<h1>Adapt the demo program to your own needs</h1>
<a href="/software/rcc_demo2/CUSTOMIZE_D.md">==> Deutsche Version</a>&nbsp; &nbsp; &nbsp; 
</td></tr></table>    

# Introduction
For many applications of the RCC system, it is sufficient to specify the components used and their wiring in the [configuration file `src/dcc_config.h`](#x20) and to adapt the text of the information pages at program start in the [file `src/rcc_demo2.text.h`](#x30).   
The control program `rcc_demo2.cpp` does not normally need to be changed. If you want to extend the control system, you will find a detailed description of the demo software under [/software/rcc_demo2/DETAILS_E.md](/software/rcc_demo2/DETAILS_E.md).   

## The configuration file dcc_config.h
## Overview
In the configuration file `dcc_config.h` all essential project properties are defined such as   
* Version designation of the program (e.g. the date of the last update)   
* Information on the network used (WLAN, WiFi)   
* Implemented MQTT GET and SET messages   
* Properties of the display used   
* a possible offset for DCC addresses   
* the number of I²C I/O expanders, their names, addresses and start values   
* the number of railroad components and their type, name, DCC address, expander number and pin assignment as well as switching times   

## Example demo program “dcc_demo2”   
The electrical wiring of the components in particular must be known and mapped in the configuration file. The following wiring is assumed for the demo program `dcc_demo2`:   
* 2x I²C expanders with the names `pcf8574_out` (7-bit address 0x20) and `pcf8574_in` (7-bit address 0x21), i.e. one expander board for outputs and one expander board for inputs.   
* 1x uncoupler (name “UC”, DCC address 11) on pin 0 of the I²C expander   
* 1x two-way crossover (name “T2”, DCC address 21) on pins 1 and 2 of the I²C expanders   
* 1x three-way switch (two drives with the names “T3L” and “T3R”, DCC addresses 31 and 32) on pins 3, 4 and 5 of the I²C expanders   
* 1x traction current switch (name “DT”, DCC address 41) on pin 6 of the I²C expander   
* 1x flashing light (name “BL”, DCC address 51) on pin 7 of the I²C expander   

The following _Figure 1_ illustrates this data again.   

circuit_rcc_demo2   
_Figure 1: Wiring of the example `rcc_demo2`_   

The listing shows the configuration file for the demo program __with line numbers__. It then explains which lines need to be adapted.   

```   
1	//_____dcc_config.h______________________________khartinger_____
2	// Configure file for ESP32 railroad DCC decoder program
3	// rcc_demo2
4	//
5	// Created by Karl Hartinger, November 14, 2024
6	// Changes:
7	// 2024-11-28 Change program name
8	// 2025-01-03 Change TOPIC_BASE
9	// 2025-06-18 Add "signal"
10	// 2026-01-04 Add RC_TYPE_TX, RC_TYPE_DD
11	// Released into the public domain.
12	
13	#ifndef DCC_CONFIG_H
14	 #define DCC_CONFIG_H
15	 #include <Arduino.h>                  // String, int32_t
16	 #include "src/pcf8574/D1_class_PCF8574.h"
17	
18	//_______program version________________________________________
19	#define  VERSION_99     "2026-01-04 rcc_demo2"
20	#define  VERSION_99_1   "Version 2026-01-04"
21	
22	#define  SHOW_INFOPAGE_SEC  20             // time to show one page
23	
24	//_______Network and MQTT data__________________________________
25	#define  _USE_WIFI_     true
26	#define  _SSID_         "Raspi11"
27	#define  _PASS_         "12345678"
28	#define  _HOST_         "10.1.1.1"
29	#define  TOPIC_BASE     "rcc/demo1"
30	#define  TOPIC_GET      "?,help,version,ip,signal,topicbase,eeprom,byname,bydcc,status"
31	#define  TOPIC_SET      "topicbase,eeprom0"
32	#define  TOPIC_SUB      ""
33	#define  TOPIC_PUB      ""
34	
35	//_______1.54" display data (SSD1309, 128x64 pixel, I2C)________
36	#define  SCREEN_TITLE   "RCC_Demo1"
37	#define  SCREEN_LINE_MAX 6
38	#define  SCREEN_LINE_LEN 21
39	
40	//_______DCCex__________________________________________________
41	#define  DCC_OFFSET     4
42	
43	//_______Hardware: IO expander PCF8574__________________________
44	#define  IOEX_NUM       2              // number of IO expander
45	PCF8574  pcf8574_out(1,0x20,0xFF);     // 8 digital OUT
46	PCF8574  pcf8574_in (1,0x21,0xFF);     // 8 digital IN
47	PCF8574 *pIOEx[IOEX_NUM]={&pcf8574_out, &pcf8574_in}; // IO expander
48	
49	//_______Definitions for railroad components____________________
50	//.......values for every railroad component....................
51	// e.g. turnout, uncoupler, disconnectable track, ...
52	#define  NO_PIN         -1   // no pin @ PCF8574 (0...7)
53	#define  RC_TYPE_UC     1    // uncoupler (Entkuppler)
54	#define  RC_TYPE_TO     2    // turnout (Weiche)
55	#define  RC_TYPE_T3     3    // 3way turnout (Dreiwegweiche)
56	#define  RC_TYPE_DT     4    // disconnectable track (Fahrstrom)
57	#define  RC_TYPE_TX     5    // double slip turnout/switch (Doppelkreuzungsweiche)
58	#define  RC_TYPE_DD     6    // double pole, double throw (2x UM)
59	#define  RC_TYPE_BL     9    // blink light (Blinklicht)
60	
61	//.......All properties of a railroad component.................
62	struct strRcomp {
63	  int    type;          // RC_TYPE_TO, RC_TYPE_UC, RC_TYPE_DT
64	  String name;          // short name like T1, U1, D1, W1, E1...
65	  int    dcc;           // dcc address of the component
66	  int    outPCF;        // aIOEx index of PCF8574 output device
67	  int    outBitA;       // bit PCF8574 for turnout straight (Gerade)
68	  int    outBitB;       // bit PCF8574 for turnout curved (Abzweig)
69	  int    inPCF;         // aIOEx index of PCF8574 input device
70	  int    inBitA;        // bit number at PCF8574 input straight=1
71	  int    inBitB;        // bit number at PCF8574 input curved=1
72	  int32_t msOn;         // ms on
73	  int32_t msOff;        // ms off
74	};
75	
76	//_______Railroad commands______________________________________
77	// railroad components:  type,name (max 3 char),dcc,
78	//                      pIOEx-out-index,outBitA,outBitB, 
79	//                      pIOEx-in-index inBitA inBitB
80	//                      msOn,msOff
81	// railroad component name max. 3 chars
82	// ------uncoupler (Entkuppler)---------------------------------
83	#define  RCOMP_1        RC_TYPE_UC,"UC", 11, EX0,PIN0,NO_PIN, EX1,PIN0,NO_PIN, 1500,0
84	// ------two way turnout (Zweiwegweiche = Standardweiche)-------
85	// Two expander pins A B to control 2way turnout (active low!)
86	// A=0: curved, B=0: straight
87	#define  RCOMP_2        RC_TYPE_TO,"T2", 21, EX0,PIN1,PIN2,   EX1,PIN1,PIN2, 500,0
88	//-------three way turnout (Dreiwegweiche)----------------------
89	// A=0: curved, B=0: straight (@ 3 pin: middle pin=0V -> straight)
90	#define  RCOMP_3L       RC_TYPE_T3,"T3L",31, EX0,PIN3,PIN4,   EX1,PIN3,PIN4, 500,0
91	#define  RCOMP_3R       RC_TYPE_T3,"T3R",32, EX0,PIN5,PIN4,   EX1,PIN5,PIN4, 500,0
92	//-------disconnectable track (Fahrstrom)-----------------------
93	#define  RCOMP_4        RC_TYPE_DT,"DT", 41, EX0,PIN6,NO_PIN, EX1,PIN6,NO_PIN, 0,0
94	//-------blink light (Blinklicht)-------------------------------
95	#define  RCOMP_5        RC_TYPE_BL,"BL", 51, EX0,PIN7,NO_PIN, EX1,NO_PIN,NO_PIN, 500,500
96
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

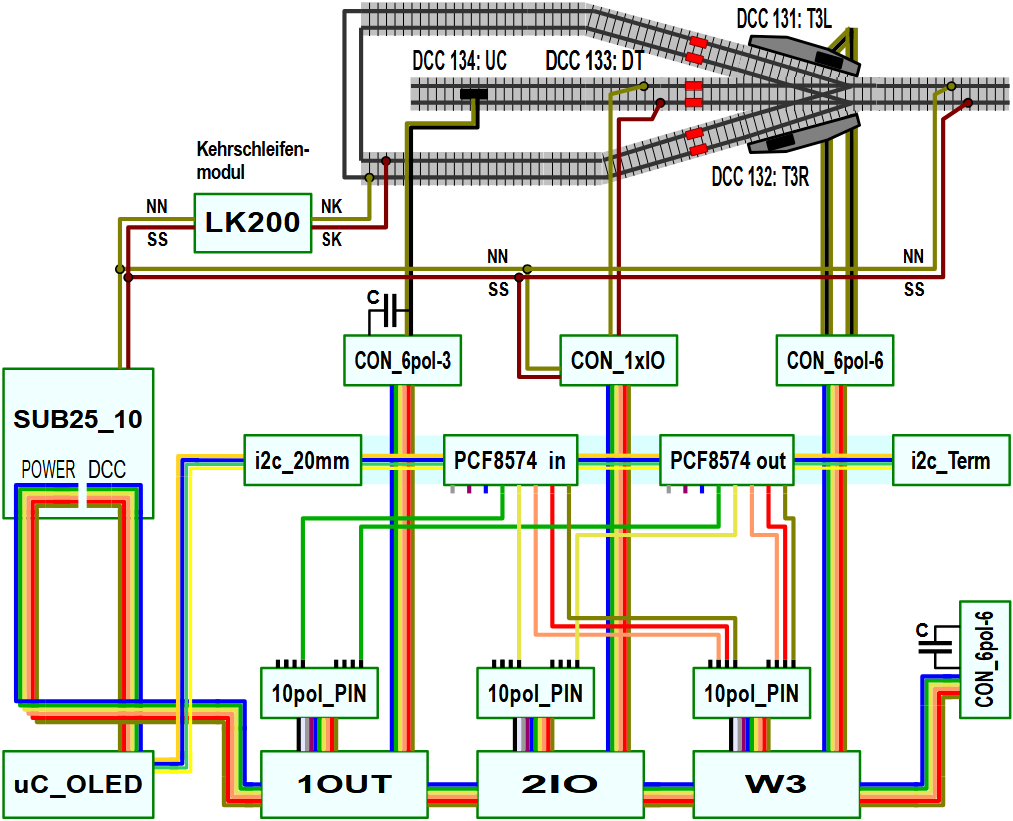
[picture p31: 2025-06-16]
examples/module13/images/o_m13_overview.png

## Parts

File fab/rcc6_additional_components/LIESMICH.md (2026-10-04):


<table><tr><td></td><td>
<h1>Weitere RCC Komponenten</h1><b><big>RCC6: Optionale Komponenten für das RCC-System</big></b><br>  
Stand: 27.9.2026    &nbsp; &nbsp; &nbsp; &nbsp;
<a href="#TableOfContents">→ Inhaltsverzeichnis</a>&nbsp; &nbsp; &nbsp; &nbsp;
<a href="README.md">→ English version</a>
</td></tr></table>

# Worum geht es?
Dieses Verzeichnis enthält optionale Komponenten für das RCC-System (RCC = Railway Component Control). Sie ergänzen das System, sind für die eigentliche Steuerung aber nicht notwendig.   

##  Inhalt
1. [RGY-Anzeige `RCC_RGY_TVn_LED`](#x10)  
2. [Pulsflanken-Erkennung Typ 1](#x20)  
3. [Set-/Reset-Pulsflanken-Erkennung (Typ 2)](#x30)  
4. [DCC-Fahrstromerkennung **ohne** Schalten](#x40)   
5. [UI-Steuerungsplatine `RW_5V_UI_STRG`](#x50)   
---
6. [Ältere Platinen mit Gleisspannungssignal TRV = 5 V](#xold)   

# 1. RGY-Anzeige

## 1.1 Einleitung

Das Board `RCC_RGY_TVn_LED` ist eine **41 × 41 mm²** große Anzeigeplatine passend zu RCC-Blöcken.  
Sie enthält bis zu **drei parallel geschaltete rot/grün-Duo-LEDs** und optional zwei Taster.  

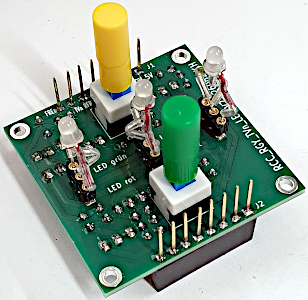
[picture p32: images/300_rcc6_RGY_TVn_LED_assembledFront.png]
rcc6_RGY_TVn_LED_Front
   

Die LEDs zeigen den Zustand der Eingangssignale **TVn** und **FREn** an.  

| TVn | FREn | LED-Farbe | LED | ROKn | RFR |  
|:---:|:----:|:---:|:---:|:---:|:---:|
| 0 V |  0 V | Grün | 🟢 | 0 V | 5 V |  
| 0 V |  5 V | Gelb (Orange) | 🟡 | 0 V | 0 V |  
| 5 V |  0 V | Rot | 🔴 | 5 V | 0 V |  
| 5 V |  5 V | Rot | 🔴 | 5 V | 0 V |  

### Bedeutung der Eingänge

- **TVn** – Gleisspannung vorhanden (*Track Voltage*, 0 V)  
- **FREn** – Gleis frei (*Track Free*, 0 V)  

Damit zeigt die Platine zum Beispiel den Zustand eines Gleises an:  

- 🟢 **Grün:** Gleis ist frei.
- 🟡 **Gelb:** Gleis ist besetzt.
- 🔴 **Rot:** Es liegt ein Fehler vor (kein Fahrstrom etc.).

### Rückmeldesignale

Zusätzlich zur LED-Anzeige stehen zwei Rückmeldesignale zur Verfügung:  

- **ROKn** – Rückmeldung ist gültig (*Response OK* = *Response Valid*, 0 V)  
- **RFRE** – Gleis ist frei (*Response Track Free*, 5 V)  

**Anmerkung**: Das Ausgangssignal RFRE ist gegenüber FREn invertiert.   

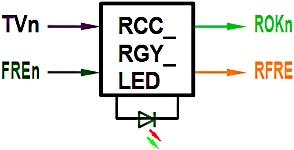
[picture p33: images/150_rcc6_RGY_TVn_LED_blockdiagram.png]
rcc6_RGY_TVn_LED_blockdiagram
   

### Optionale Taster

An den Positionen **SW1** und **SW3** können optional Taster oder Schalter eingebaut werden. Diese können von einer Steuerplatine ausgewertet werden, zum Beispiel zum Testen der **SET-** und **RESET-Eingänge** einer [Pulsspeicher-Steuerungsplatine `RCC_PULS2_STRG`](#x30).

## 1.2 Schaltplan
Die RGY-Anzeige besteht aus drei Teilen:   
1. Die LED-Anzeige   
2. die Rückmeldeschaltung   
3. Zwei Taster für Testzwecke   

### Led-Anzeige
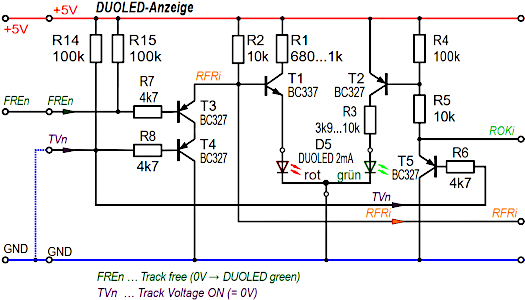
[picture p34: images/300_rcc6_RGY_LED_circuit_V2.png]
rcc6_RGY_LED_circuit
   

Die Ansteuerung der Platine erfolgt über die Signale **TVn** (J1-Pin 7) und **FREn** (J1-Pin 8):   
- TVn = 5 V: Led leuchtet rot.  
  (Transistor T4 sperrt, T1 leitet → "LED rot"; T5 sperrt, T2 sperrt)  
- TVn = 5 V und FREn = 5 V: LED leuchtet gelb.  
  (T4 leitet, T3 sperrt, T1 Leitet → "LED rot"; T5 leitet, T2 leitet → "LED grün" → = rot + grün = gelb).  
- TVn = 5 V und FREn = 0 V: LED leuchtet grün.  
   (T4 leitet, T3 leitet, T1 sperrt; T5 leitet, T2 leitet → "LED grün")  

__Anmerkungen__
* Widerstand R1: 680 Ω bei drei Duo-LEDs, 1 kΩ bei einer Duo-LED   
* Widerstand R3: 3,9 kΩ bei drei Duo-LEDs, 10 kΩ bei einer Duo-LED   

### Rückmeldeschaltung
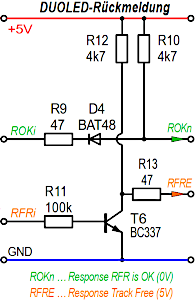
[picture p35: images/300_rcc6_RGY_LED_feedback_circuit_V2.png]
rcc6_RGY_LED_feedback_circuit
   

#### OK-Rückmeldung (ROKn)

Das interne Signal **ROKi** wird für den externen Ausgang (**ROKn**) etwas aufbereitet.   

- Die Diode **D4** verhindert, dass die Duo-LED belastet wird, wenn der Transistor **T5** gesperrt ist. Gleichzeitig zieht **R10** den Ausgang **ROKn** auf **5 V**.   
- Schaltet **T5** durch, begrenzt **R9** einen möglichen Fehlerstrom von außen.   

#### Gleisfrei-Rückmeldung (RFR)

Das interne Signal **RFRi** wird mit dem Transistor **T6** invertiert und als **RFRE** ausgegeben.   

### Optionale Taster oder Schalter

Auf der Platine können an den Positionen **SW1** und **SW3** optional Taster oder Schalter eingebaut werden.  

Im Ruhezustand sind die Ausgänge **offen**.  
Beim Betätigen werden sie mit **0 V (Masse)** verbunden.  

### Gesamtschaltplan

KiCad-Schaltplan der Platine **`RCC_RGY_TVn_LED`**:   
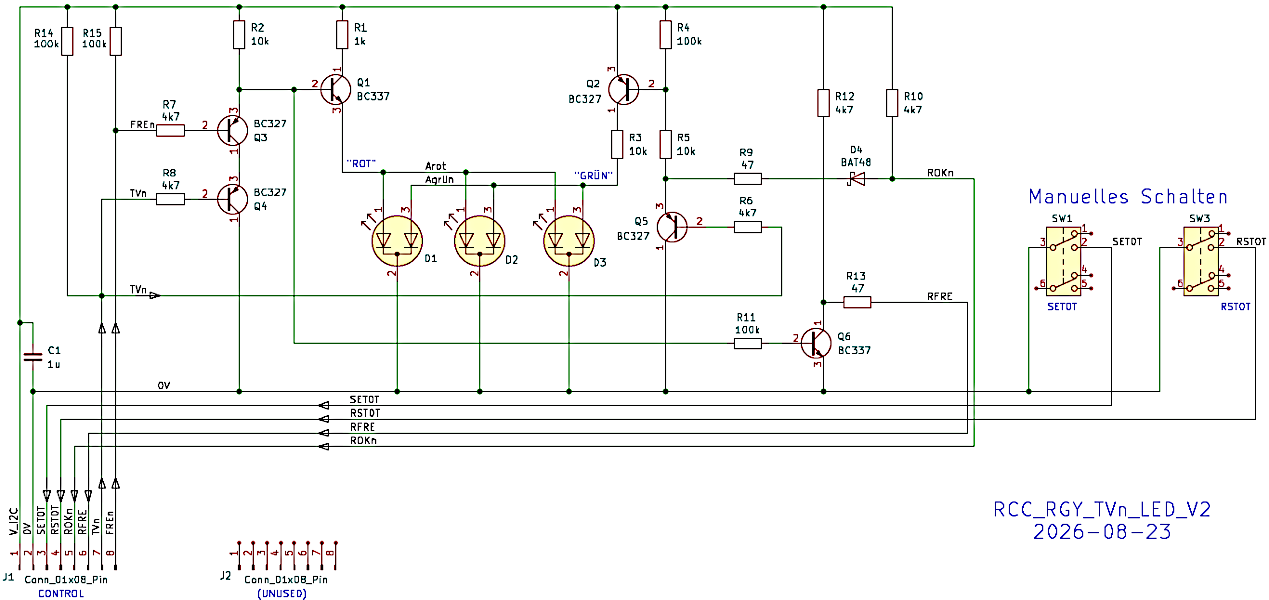
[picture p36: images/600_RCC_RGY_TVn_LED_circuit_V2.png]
RCC_RGY_TVn_LED_circuit
  

Die Stromversorgung und alle Ein- und Ausgangssignale befinden sich an der Stiftleiste J1.  

## 1.3 Bestückung der Platine
Bild der Platine "`RCC_RGY_TVn_LED`" (Version 1):   
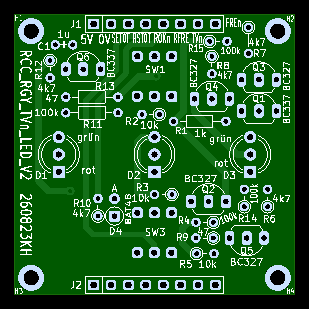
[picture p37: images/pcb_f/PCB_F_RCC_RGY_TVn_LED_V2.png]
Platine RW_5V_RGY_LED
   

Best&uuml;ckte Platine "`RCC_RGY_TVn_LED`"   
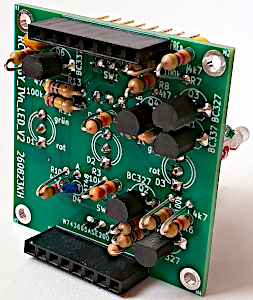
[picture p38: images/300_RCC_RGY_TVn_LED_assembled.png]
Bestückte Platine RW_5V_RGY_LED
   

### St&uuml;ckliste   

| Anzahl | Referenz | Wert | Geh&auml;use | 
|-----|-----|-----|-----|
| 1 | C1 | Kondensator 1 &micro;F, 16 V, Raster 2,54 mm | C_L4mm_D3mm_P2.54mm_kh | 
| 3 | D1, D2, D3 | Dual-LED rot-gr&uuml;n, gemeinsame Kathode | LED_D5.0mm-3 | 
| 3 | D1, D2, D3 | Buchsenleiste 3-polig mit gedrehten Pins | "Fassung" f&uuml;r LEDs | 
| 1 | D4 | Diode BAT48 | D_DO-35_SOD27_P2.54mm_Vertical_AnodeUp | 
| 2 | J1, J2 | Buchsenleiste 8-polig mit langen Kontakten (Conn_01x08_Pin) | PinSocket_1x08_P2.54mm_Vertical_11mm_kh | 
| 4 | Q1, Q6 | Transistor BC337-40 (npn) | TO-92_Inline_Wide_custom | 
| 2 | Q2, Q3, Q4, Q5 | Transistor BC327-40 (pnp) | TO-92_Inline_Wide_custom | 
| 1 | R1 | 680 &Omega;..1 k&Omega; (2) | R_Axial_DIN0204_L3.6mm_D1.6mm_P7.62mm_Horizontal | 
| 1 | R11 | 100 k&Omega; | R_Axial_DIN0204_L3.6mm_D1.6mm_P7.62mm_Horizontal | 
| 1 | R3 | 3,9 k&Omega;..10 k&Omega; (3) | R_Axial_DIN0204_L3.6mm_D1.6mm_P2.54mm_Vertical_kh | 
| 1 | R13 | 47 &Omega; | R_Axial_DIN0204_L3.6mm_D1.6mm_P7.62mm_Horizontal | 
| 1 | R9 | 47 &Omega; | R_Axial_DIN0204_L3.6mm_D1.6mm_P2.54mm_Vertical_kh | 
| 4 | R6, R8, R10, R12 | 4,7 k&Omega; | R_Axial_DIN0204_L3.6mm_D1.6mm_P2.54mm_Vertical_kh | 
| 1 | R7 | 4,7 k&Omega; | R_Axial_DIN0204_L3.6mm_D1.6mm_P3.81mm_Vertical_kh | 
| 2 | R2, R5 | 10 k&Omega; | R_Axial_DIN0204_L3.6mm_D1.6mm_P2.54mm_Vertical_kh | 
| 3 | R4, R14, R15 | 100 k&Omega; | R_Axial_DIN0204_L3.6mm_D1.6mm_P2.54mm_Vertical | 
| 2 | SW1, SW3 | Taster SW_Push_DPDT_8x8 | SW_Push_DPDT_8x8 | 
| 2 | SW1, SW3 | Knopf f&uuml;r Taster/Schalter 8x8mm, L&auml;nge 10mm, Farbe je nach Anwendung | 

### Anmerkungen
(1) Es ist sinnvoll, die 3-poligen Buchsenleisten an alle 3 LED-Positionen zu l&ouml;ten, auch wenn im Betrieb weniger LEDs eingesetzt werden.  
(2) Widerstand R1: **680 &Omega;** bei drei Duo-LEDs, 1 k&Omega; bei einer Duo-LED   
(3) Widerstand R3: **3,9 k&Omega;** bei drei Duo-LEDs, 10 k&Omega; bei einer Duo-LED   
   
### Vorbereitung
1. Von einer langen, einreihigen Buchsenleiste 3x 3-polige St&uuml;cke abtrennen (f&uuml;r D1 bis D3).   
2. Die äußeren LED-Anschl&uuml;sse farblich kennzeichnen:  
   * kurzen Anschluss grün färben, mittellangen Anschluss rot  
3. Schrumpfschlauch 11 mm auf jeden LED-Anschluss aufschrumpfen  
4. LED-Anschl&uuml;sse auf 17 bis 18 mm abschneiden und Ecken biegen ("Feder", mittleren Anschluss nach vorne oder hinten). Länge dann ca. 13 mm.   
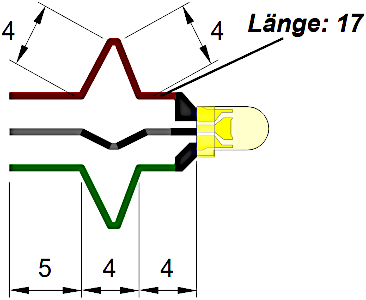
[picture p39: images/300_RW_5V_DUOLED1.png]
RW_5V_DUOLED1
 
RW_5V_DUOLED2   

4. NUR wenn Taster verwendet werden: 10 mm-Tasterkn&ouml;pfe SW1, SW2 eventuell verl&auml;ngern durch Aufkleben mit Sekundenkleber auf 7 mm-Tasterkn&ouml;pfe.   

Bauteile der Platine "RW_5V_RGY_LED"   
RW_5V_RGY_LED_parts RW_5V_RGY_STRG_parts   

### Best&uuml;ckung   
**Lötseite** (!):  

1. Die dreipoligen Buchsenleisten (D1 bis D3) mit gedrehten Pins auf die **L&ouml;tseite** des Prints l&ouml;ten.   

Auf die **Bauteilseite** l&ouml;ten:   

2. Widerstände R1, R11 und R13 (liegend, **680 &Omega;** ... 1 k&Omega;, 100 k&Omega;, 47 &Omega;)   
3. Transistoren Q1, Q6 (BC337-40)   
4. Transistoren Q2, Q3, Q4, Q5 (BC327-40)   
5. Kondensator C1 (1 &micro;F)   
6. Diode D4 (BAT48, auf Polung achten: Kathode unten beim Kreis)   
7. Widerstand R3 (**3,9 k&Omega;** ... 10 k&Omega;)   
8. Widerstand R9 (47 &Omega;)
9. Widerst&auml;nde R6, R7, R8, R10, R12 (4,7 k&Omega;, stehend)   
10. Widerst&auml;nde R2, R5 (10 k&Omega;, stehend)   
11. Widerst&auml;nde R4, R14, R15 (100 k&Omega;, stehend)   
12. Buchsenleisten 8-polig mit langen Kontakten J1 und J2   

Optional: Auf die **L&ouml;tseite** l&ouml;ten:   

13. Taster SW1, SW3   

### Print vervollständigen
Duo-LED(s) einstecken (auf Polung achten).   

## 1.4 Test
### Vorbereitung
* 5x Kabel Stecker-Buchse (schwarz, rot, gelb, grün, violett)   
* Steckbrett zum Verteilen der 0V und 5V
* Netzgerät 5 V   
* Voltmeter (Bereich 20VDC)   

### Durchführung
Print auf die Bauteilseite legen. Alle erforderlichen Anschlüsse befinden sich an den langen Kontakten der der Buchsenleiste J1:   

rcc6_RGY_LED_J1   

1. Versorgungsspannung am Steckbrett anschließen.

2. Versorgungsspannung am Board anlegen: Pin 1 mit 5V, Pin 2 mit GND verbinden:   
   ► 🔴🔴🔴 Die LEDs leuchten rot.   

3. Voltmeter an GND anschließen. Messen:  
   ► Pin 5 = ROKn = +5V  
   ► Pin 6 = RFR = 0V   

4. Pin 7 = TVn mit 0 V verbinden (active low):   
   ► 🟡🟡🟡 Die LEDs leuchten gelb (orange).   

5. Messen:  
   ► Pin 5 = ROKn = 0,9V  
   ► Pin 6 = RFRE = 0,1V  

6. Pin 8 = FREn mit 0V verbinden:   
   ► 🟢🟢🟢 Die LEDs leuchten grün.   

7. Messen:  
   ► Pin 5 = ROKn = 0,9V  
   ► Pin 6 = RFRE = 3,8V  

## 1.5 Hinweise zur Montage
Duo-LEDs mit drei Anschlüssen passen nicht in Standard-LED-Fassungen.  
Die Montage des `RCC_RGY_TVn_LED`-Boards erfolgt daher mit dem Board `RW_LEER_DUOLED`. Bei diesem sind die Bohrungen für LED2 und LED5 vergrößert.   
Steht kein `RW_LEER_DUOLED`-Board zur Verfügung, kann man auch das `RW_LEER_LED`-Board verwenden und die Bohrungen LED2 und LED5 auf 8 mm aufbohren (gleich groß wie die Bohrungen für die Taster).

Befestigungsplatine DUOLED Befestigungsplatine DUOLED auf RGY_LED Befestigungsplatine DUOLED auf RGY_LED   

## 1.6 Versionen
* V1 (260820): OK  
* V2 (260823): OK  

# 2. Puls-Erkennung Typ 1

## 2.1 Prinzip

Die Puls-Erkennung Typ 1 (kurz "PULS1") reagiert auf eine fallende Flanke am Eingang und erzeugt einen Puls vorgegebener Länge. Die Pulslänge ist mit einem Potenziometer zwischen Millisekunden und Sekunden einstellbar. Es sind zwei voneinander unabhängige Kanäle verfügbar.  
Bleibt ein Impulseingang länger auf 0, so bleibt auch das Ausgangssignal auf 0.  

## 2.2 Steuerung Puls-Erkennung Typ 1 (`RCC_PULS1_STRG`)

### Schaltplan
Schaltplan RCC_PULS1_STRG  

### St&uuml;ckliste   
| Anzahl | Referenz | Wert | Geh&auml;use | 
|-----|-----|-----|-----|
| 2 | C1, C2 | 100 nF, 5,08 mm | C_Rect_L7.0mm_W2.0mm_P5.00mm_kh | 
| 2 | C3, C4 | Tantal-Elko 10 &micro;F, 16 V, 2,54 mm| ELKO_L4.32mm_D3.81mm_P2.54mm_kh | 
| 3 | D1, D2, D3 | BAT48 | D_DO-35_P2.0mm_Vertical_AnodeUp_kh | 
| 7 | D4, D5, D6, D7, D8, D9, D10 | BAT48 | D_DO-35_SOD27_P2.54mm_Vertical_AnodeUp_kh | 
| 2 | J1, J2 | Stiftleiste 8-polig (Conn_01x08_Pin) | PinSocket_1x08_P2.54mm_Vertical_kh | 
| 2 | J3, J5 | Wannenstecker 6-polig, stehend | Box_02x03_P2.54mm_Vertical_kh | 
| 1 | J4 | Wannenstecker 10-polig, stehend | Box_02x05_P2.54mm_Vertical_kh | 
| 2 | Q1, Q2 | npn-Transistor BC337 | TO-92_Inline_Wide_custom | 
| 2 | R7, R8 | 1 k&Omega; | R_Axial_DIN0204_L3.6mm_D1.6mm_P2.54mm_Vertical_kh | 
| 1 | R3 | 4,7 k&Omega;| R_Axial_DIN0204_L3.6mm_D1.6mm_P2.54mm_Vertical | 
| 1 | R4 | 4,7 k&Omega; | R_Axial_DIN0204_L3.6mm_D1.6mm_P3.81mm_Vertical_kh | 
| 2 | R1, R5 | 10 k&Omega; | R_Axial_DIN0204_L3.6mm_D1.6mm_P2.54mm_Vertical | 
| 2 | R2, R6 | 10 k&Omega; | R_Axial_DIN0204_L3.6mm_D1.6mm_P2.54mm_Vertical_kh | 
| 2 | RV1, RV2 | Trimmer 500 k&Omega; stehend | Trim_RM-063_Horizontal_kh | 
| 1 | U1 | CD4538  Dual Precision Monostable Multivibrator (Monoflop), retriggerbar |  | 
| 1 | U1 | IC-Fassung 16-polig, gedrehte Pins | DIP-16_W7.62mm_kh | 

### Bestückung
1. IC-Fassung U1 (auf Polung = Kerbe achten)  
2. Dioden D1 bis D10 (stehend, auf Polung achten: Kathode im weißen Kreis!)  
3. Transistoren Q1, Q2 (BC337)  
4 Tantal-Elko C3, C4 (auf Polung achten!)  
5 Trimmer RV1, RV2  
6. Alle Widerstände R1 bis R8  
7. Kondensatoren C1, C2 (100 nF)  
8. Wannenstecker J3 bis J5 (auf Polung achten!)  

Auf die _*L&ouml;tseite*_ l&ouml;ten:   
9. Stiftleisten J1 und J2 NACH UNTEN anl&ouml;ten!   

## Versionen
* V1 (260824): OK  

## 2.3 LED-Anzeige Puls-Erkennung Typ 1 (`RCC_PULS1_LED`)

### Schaltplan
Schaltplan RCC_PULS1_LED  

### St&uuml;ckliste   
| Anzahl | Referenz | Wert | Geh&auml;use | 
|-----|-----|-----|-----|
| 1 | C1 | Kondensator 100 nF | C_L4mm_D3mm_P2.54mm_kh | 
| 2 | D1, D4 | LED gelb | LED_D3.0mm | 
| 2 | D2, D5 | LED grün | LED_D3.0mm | 
| 4 | D1, D2, D4, D5 | Buchsenleiste (gedrehte Buchsen), 2-polig (1) | | 
| 2 | J1, J2 | Buchsenleiste 8-polig mit langen Kontakten (Conn_01x08_Pin) | PinSocket_1x08_P2.54mm_Vertical_11mm_kh | 
| 2 | Q1, Q2 | npn-Transistor BC337 | TO-92_Inline_Wide_custom | 
| 1 | R5 | 47 &Omega; | R_Axial_DIN0204_L3.6mm_D1.6mm_P2.54mm_Vertical_kh | 
| 1 | R10 | 47 &Omega; | R_Axial_DIN0204_L3.6mm_D1.6mm_P2.54mm_Vertical | 
| 3 | R1, R6, R8 | 1 k&Omega; | R_Axial_DIN0204_L3.6mm_D1.6mm_P10,16mm_Horizontal | 
| 1 | R3 | 1 k&Omega; | R_Axial_DIN0204_L3.6mm_D1.6mm_P2.54mm_Vertical_kh | 
| 2 | R4, R9 | 10 k&Omega; | R_Axial_DIN0204_L3.6mm_D1.6mm_P2.54mm_Vertical_kh | 
| 1 | R2 | 100 k&Omega; | R_Axial_DIN0204_L3.6mm_D1.6mm_P3.81mm_Vertical_kh | 
| 1 | R7 | 100 k&Omega; | R_Axial_DIN0204_L3.6mm_D1.6mm_P7.62mm_Horizontal | 

#### Vorbereitung   
1. 4x gedrehte, 2-polige Buchsen für die LEDs: Von einer (meist 40-poligen) Buchsenleiste herunterschneiden.   
2. Die LED-Anschl&uuml;sse entsprechend [Kapitel 1.4](#x14) abschneiden und biegen.   

### Bestückung
1. Die zweipoligen Buchsenleisten (D1, D2, D4, D5) mit gedrehten Pins auf die _L&ouml;tseite_ des Prints l&ouml;ten.   

Auf die _*Bauteilseite*_ l&ouml;ten:   
2. Widerstände R1, R6, R8 (1 k&Omega; liegend, 10 mm)  
3. Widerstand R7 (100 k&Omega; liegend, 7,6 mm)  
4. Transistoren Q1, Q2 (BC337)   
5. Kindensator C1 (100 nF, 2,54 mm Raster)  
6. Widerstände R5, R10 (47 &Omega;, stehend)  
7. Widerstand R3 (1 k&Omega;, stehend)  
8. Widerstände R4, R9 (10 k&Omega;, stehend)  
9. Widerstand R2 (100 k&Omega;, stehend)  
10. Buchsenleisten J1 und J2   

### Versionen
* V1 (260824): OK  

## 2.4 Zusammenbau des PULS1-Blocks
1. Aufstecken des Steuerungsboards `RCC_PULS1_STRG` auf das Anzeigeboard `RCC_PULS1_LED`.   
2. Einstecken der LEDs. F&uuml;r alle LEDs gilt: Anode = Pluspol = rot markiert immer __nach au&szlig;en__ zum Leiterplattenrand.   
3. Falls vorhanden: Print `RW_LEER_LED` auf das Anzeigeboard stecken.   

## 2.5 Test des PULS1-Blocks
### Pinbelegung der Stecker am STRG-Board
Pinbelegung PULS1 Stecker J4 J5  

### Vorbereitung
(1) Stecke ein 6-poliges Flachbandkabel am **6-poligen Stecker J5-Pin 1** an und stecke am anderen Kabelende einen Stift-Stift-Draht in **Pin 1** (Reedkontakt-Eingang 1).  
   Oder: Stecke DIREKT am **6-poligen Stecker J5-Pin 1** einen Buchsen-Buchsen-Draht an.  
(2) Lege an den PULS1-Block die Versorgungsspannung an (6-poliger Stecker J3)  
   ► die beiden grünen LEDs 🟢 leuchten

### Testdurchführung
#### Puls-Eingang 1
* Verbinde J5-Pin 1 kurz mit GND an J5-Pin 5:  
  ► die linke, gelbe LED 🟡 leuchtet kurz auf.  
  Die Leuchtdauer kann mit dem Trimmer RV1 eingestellt werden.  

Bleibt der Eingang länger auf 0, so bleibt auch das Ausgangssignal so lange auf 0.  

#### Puls-Eingang 2
* Verbinde J5-Pin 2 kurz mit GND an J5-Pin 5:  
  ► die rechte, gelbe LED 🟡 leuchtet kurz auf.  
  Die Leuchtdauer kann mit dem Trimmer RV2 eingestellt werden.  

Bleibt der Eingang länger auf 0, so bleibt auch das Ausgangssignal so lange auf 0.  

#### I²C-Rückmeldung
**Kanal 1**  
* Verbinde das Voltmeter mit J4-Pin 1 (V) und J4-Pin 5 (COM = GND = 0V):  
  ► Anzeige 5 V  
* Erzeuge einen Puls am Eingang 1, d.h. verbinde J5-Pin 1 kurz mit GND an J5-Pin 5:  
  ► Anzeige 0 V, solange der Puls dauert.  

Führe den Test auch für Kanal 2 durch.  

# 3. Set-/Reset-Pulsflanken-Erkennung (Typ 2)

## 3.1 Prinzip

Die Puls-Erkennung Typ 2 (kurz "PULS2") reagiert auf fallende Flanken am SET- und RESET-Eingang. Der letzte Zustand wird gespeichert und steht auch nach einem Stromausfall zur Verfügung.  

### Eingänge

SET- und RESET-Eingang können auf 3 Arten getriggert werden:  
* 6-poliger Stecker J5  
* Taster (zB auf Platine `RCC_RGY_TVn_LED`)  
* 10-poliger Stecker J4 (I²C-Anschluss)  

RW_5V_PULS_STRG_IN   

### Ausgänge

Die Pulsspeicher-Steuerungsplatine `RCC_PULS_TVn_STRG` erzeugt  
* die Steuersignale `FREn` und `TVn` für die LED-Anzeige und   
* leitet die LED-Anzeige-Rückmeldung `ROKn` und `RFRE` zum I²C-Stecker J4 weiter.   

Zur Anzeige wird das Board `RCC_RGY_TVn_LED` verwendet.   

## 3.2 Steuerung Puls-Erkennung Typ 2 (`RCC_PULS2_TVn_STRG`)

### 3.2.1 Schaltplan
Die Puls-Steuerung besteht aus 5 Stufen:   
* Eingänge  
* Impulserzeugung  
* Flipflop (HEF4093)  
* H-Brücken-Treiber (DRV8833)  
* Bistabiles Relais (IM41)  

KiCad-Schaltplan der Platine "RCC_PULS2_TVn_STRG" (Version 1):   

RCC_PULS2_TVn_STRG_circuit   

### 3.2.2 Bestückung der Platine
Bild der Platine `RCC_PULS2_TVn_STRG` (Version 1):   
PULS2-Platine   

Best&uuml;ckte Platine "RCC_PULS2_TVn_STRG_V1"   
RCC_PULS2_TVn_STRG bestückt1 RCC_PULS2_TVn_STRG  

#### St&uuml;ckliste   
| Anzahl | Referenz | Wert | Geh&auml;use | 
|-----|-----|-----|-----|
| 3 | C1, C2, C4 | 100 nF, Raster 2,54 mm | C_L4mm_D3mm_P2.54mm_kh | 
| 2 | C3, C5 | 10 nF, Raster 2,54 mm | C_L4mm_D3mm_P2.54mm_kh | 
| 1 | C6 | Elko 10 &micro;F, 16 V, Raster 2,54 mm | ELKO_L7.88mm_D4.57mm_P2.54mm_kh | 
| 3 | D1, D2, D4 | BAT48 | D_DO-35_P1.778mm_Vertical_AnodeUp_kh | 
| 2 | D3, D6 | BAT48 | D_DO-35_SOD27_P5.08mm_Horizontal_kh | 
| 3 | D5, D8, D9 | BAT48 | D_DO-35_P2.0mm_Vertical_AnodeUp_kh | 
| 1 | D7 | BAT48 | D_DO-35_SOD27_P2.54mm_Vertical_AnodeUp | 
| 2 | J1, J2 | Stiftleiste 8-polig (Conn_01x08_Pin) | PinSocket_1x08_P2.54mm_Vertical_Back_kh | 
| 2 | J3, J5 | Wannenstecker 6-polig, stehend | Box_02x03_P2.54mm_Vertical_kh | 
| 1 | J4 | Wannenstecker 10-polig, stehend | Box_02x05_P2.54mm_Vertical_kh | 
| 1 | J6 | DRV8833_Board [1] | DRV8833_Board | 
| 2 | J6 | Buchsenleiste 6 Pin [2] | | 
| 1 | J7 | Stiftleiste 2-polig (Jumper_2) [3] | PinSocket_1x02_P2.54mm_Vertical_kh | 
| 1 | J7 | Jumper (2-polig) | | 
| 1 | K1 | Relais IM41, 3 V, 2x UM, bistabil | Relay_DPDT_AXICOM_IMSeries_Pitch5.08mm_rect_Pins | 
| 2 | R21, R24 | 100 &Omega; | R_Axial_P1.778mm_Vertical_kh | 
| 2 | R28, R29 | 100 &Omega; | R_Axial_DIN0204_L3.6mm_D1.6mm_P2.54mm_Vertical_kh | 
| 4 | R22, R23, R25, R26 | 100 k&Omega; | R_Axial_P1.778mm_Vertical_kh | 
| 1 | R27 | 100 k&Omega; | R_Axial_DIN0204_L3.6mm_D1.6mm_P7.62mm_Horizontal | 
| 1 | U1 | 4-fach NAND mit Schmitt-Trigger HEF4093B | DIP-14_W7.62mm_Socket_kh | 
| 1 | U1 | Fassung DIL 14 (2x7 Pin), gedrehte Kontakte | | 

Bauteile der Platine `RCC_PULS2_TVn_STRG`:   
RCC_PULS2_TVn_STRG_parts   

#### Vorbereitung
[1] 1. Auf dem DRV8833_Board J6 die Verbindung bei J1 **auftrennen**.   
&nbsp; &nbsp; &nbsp;2. 2x 6polige Stiftleisten zu den Bauteilen hin anlöten.   
[2] Von einer flachen, einreihigen Buchsenleiste 2x 6-polige St&uuml;cke abtrennen (f&uuml;r J6) oder   
    zB eine DIL 14 Fassung mit Federkontakten auseinanderschneiden und 2x 6-polige St&uuml;cke abtrennen (f&uuml;r J6).   
[3] Von einer langen, einreihigen Stiftleiste 1x 2-poliges St&uuml;ck abtrennen (f&uuml;r J7).   

#### Best&uuml;ckung   
  
1. Widerstand R27 (100 k&Omega;, liegend)   
2. Diode D3, D6 (BAT48, liegend, Kathode beim weißen Strich)   
3. Elko C6 (10 &micro;F, liegend, auf Polung achten!)   
4. Fassung U1 (DIL 14, auf Polung/Kerbe achten!)   
5. Buchsenleisten J6 (2x 6 Pin)   
6. **Bistabiles** Relais K1 (IM41, 3V, auf Polung achten)   
7. Diode D1, D2, D4, D5, D7, D8, D9 (BAT48, stehend, Kathode in den Kreis)   
8. Kondensatoren C3, C5 (10 nF = 103, Raster 2,54 mm, stehend)   
9. Kondensatoren C1, C2, C4 (100 nF = 104, Raster 2,54 mm, stehend)   
10. Stiftleiste J7 (2-polig)   
11. Widerst&auml;nde R21, R24, R28, R29 (100 &Omega;, stehend)   
12. Widerst&auml;nde R22, R23, R25, R26 (100 k&Omega;, stehend)   
13. Wannenstecker J1 bis J3 (auf Polung achten - Pin 1)   
14. Kondensator C2 (100 nF = 104, Raster 2,54 mm, stehend)   
15. Stiftleisten J1 und J2 **NACH UNTEN** anl&ouml;ten!   

#### Print vervollständigen
* Jumper auf Stifte J7 aufstecken.   
* 4-fach NAND HEF4093B einstecken.   
* DRV8833_Board aufstecken.   

## 3.2.3 Versionen
* V1 (260727): OK.   

## 3.3 Inbetriebnahme und Test

#### Pinbelegung des 6-poligen Steckers J5:   
RW_5V_PULS_STRG_J5   

#### Pinbelegung des 10-poligen Steckers J4:   
RW_5V_PULS_STRG_J4   

Der Test der Platine `RCC_PULS2_TVn_STRG` erfolgt gemeinsam mit der Platine `RCC_RGY_TVn_LED`.   

# 4. DCC-Fahrstromerkennung ohne Schalten
## 4.1 Einleitung
Die DCC-Fahrstromerkennung **ohne Schalten** besteht aus drei Platinen:  
* UI-Erkennung `dcc_track_UI_TVn_V1`  
* Steuerungsplatine (Anschlussplatine) `RCC_UI_TVn_STRG_V1`  
* Anzeigeplatine `RCC_RGY_TVn_LED_V1`  

## 4.2 UI-Erkennung `dcc_track_UI_TVn_V1` (ohne Schalten)

### 4.2.1 Funktion

Die DCC-Gleis-UI-Erkennung überwacht ein Gleis. Sie erkennt, ob  
1. **Gleisspannung** anliegt und ob  
2. **Fahrstrom** fließt.

Der Status wird über  
- **LEDs angezeigt** und steht zusätzlich an 
- **zwei digitalen Ausgängen** zur Verfügung.   

So kann man erkennen, ob ein Gleis **besetzt** ist.   

Die Stromversorgung und die beiden digitalen Ausgänge sind über einen **6-poligen Stecker** angeschlossen.   
UI_pin_J5   

TVn ... Track Voltage ON (0V) = Fahrspannung ein (0V)   
FREn ... Track Free (0V) = Gleis frei (0V)   

Die technische Funktion ist weitgehend identisch mit `RCC_TUI_EXT` (bis auf das Schalten des Fahrstroms) und ist hier beschrieben:  
[https://github.com/khartinger/RCC5V/blob/main/fab/rcc4_block/LIESMICH.md](https://github.com/khartinger/RCC5V/blob/main/fab/rcc4_block/LIESMICH.md#x72)

### 4.2.2 Gesamtschaltung

KiCad-Schaltplan der "dcc_track_UI_TVn"-Platine:   
Version 1:  
dcc_track_UI_TVn_V1_circuit   

Version 2:  
dcc_track_UI_TVn_V2_circuit   

### 4.2.3 Bestücken der Platine
Bild der Platine zur DCC-Gleis-Spannungs-/Strom-Erkennung (Version 2):   
Platine Gleis-UI-Erkennung   

Best&uuml;ckte Platine "dcc_track_UI_TVn_V1"   
Bestückte Platine dcc_track_UI_TVn   

#### St&uuml;ckliste   
| Anzahl | Referenz | Wert | Geh&auml;use | 
|---|---|---|---|
| 5 | C1, C2, C4, C7, C8 | Kondensator 1 &micro;F, 16 V, Raster 2,54 mm | C_L4mm_D3mm_P2.54mm_kh | 
| 2 | C3, C5 | Tantal-Elko 10 &micro;F, 16 V, Raster 2,54 mm | C_L4.32mm_D3.81mm_P2.54mm_kh | 
| 1 | C6 | Elko 33 &micro;F, 35 V, Raster 2,54 mm | CP_Radial_D8.0mm_P2.50mm | 
| 2 | D1, D2 | Diode SB240 | D_DO-15_P3.81mm_Vertical_AnodeUp | 
| 1 | D3 | Diode BAT48 | D_DO-35_SOD27_P2.54mm_Vertical_AnodeUp | 
| 1 | D5 | Diode 1N4007 | D_DO-41_SOD81_P3.81mm_Vertical_AnodeUp_kh | 
| 1 | D4 | LED rot, 3 mm, 2 mA | LED_D3.0mm | 
| 1 | D6 | LED gr&uuml;n, 3 mm, 2 mA | LED_D3.0mm | 
| 2 | D4, D6 | gedrehte Buchsen, 2-polig | | 
| 2 | J1, J2 | Schraubklemme, 2-polig, schwarz, 5 mm | Screw_Terminal_01x02_P5 | 
| 1 | J3 | Stiftleiste 2-polig | PinSocket_1x02_P2.54mm_Vertical_kh | 
| 1 | J3 | Jumper 2-polig | | 
| 1 | J5 | Wannenstecker 6-polig, stehend | Box_02x03_P2.54mm_Vertical_kh | 
| 1 | Q1 | npn-Transistor BC337-40 | TO-92_Inline_Wide_custom | 
| 1 | Q2 | pnp-Transistor BC327-40 | TO-92_Inline_Wide_custom | 
| 2 | R16, R18 | 47 &Omega;| R_Axial_DIN0204_L3.6mm_D1.6mm_P2.54mm_Vertical_kh | 
| 1 | R11 | 100 &Omega; | R_Axial_DIN0204_L3.6mm_D1.6mm_P2.54mm_Vertical | 
| 4 | R4, R8, R10, R13 | 1 k&Omega; | R_Axial_DIN0204_L3.6mm_D1.6mm_P2.54mm_Vertical_kh | 
| 1 | R12 | 1 k&Omega; | R_Axial_DIN0204_L3.6mm_D1.6mm_P2.54mm_Vertical | 
| 2 | R14, R15 | 4,7 k&Omega; | R_Axial_DIN0204_L3.6mm_D1.6mm_P2.54mm_Vertical_kh | 
| 1 | R1 | 10 k&Omega; | R_Axial_DIN0204_L3.6mm_D1.6mm_P7.62mm_Horizontal | 
| 2 | Rs2, Rs3 | 100 k&Omega; (alt: 10 k&Omega;) | R_Axial_DIN0204_L3.6mm_D1.6mm_P7.62mm_Horizontal | 
| 4 | R2, R6, R7, Rs1 | 10 k&Omega; | R_Axial_DIN0204_L3.6mm_D1.6mm_P2.54mm_Vertical_kh | 
| 1 | R3 | 33 k&Omega; oder 22 k&Omega; | R_Axial_DIN0204_L3.6mm_D1.6mm_P7.62mm_Horizontal | 
| 1 | R5 | 47 k&Omega; | R_Axial_DIN0204_L3.6mm_D1.6mm_P7.62mm_Horizontal | 
| 2 | R9, R17 | 47 k&Omega; | R_Axial_DIN0204_L3.6mm_D1.6mm_P2.54mm_Vertical_kh | 
| 1 | Rs4 | 220 k&Omega; | R_Axial_DIN0204_L3.6mm_D1.6mm_P7.62mm_Horizontal | 
| 1 | RV1 | 10-Gang-Trimmer 10 k&Omega; stehend | Trim_Bourns_3296W_Vertical | 
| 1 | U1 | INA333_Board | INA333-Board | 
| 2 | U1 | Stiftleiste 4-Pin | | 
| 2 | U1 | Buchsenleiste 4-Pin | | 
| 1 | U2 | 2-fach-Komparator LM393 | DIP-8_W7.62mm_Socket_LongPads | 
| 1 | U2 | Präzisionssockel 8 Pin (2x 4 Pin, Abstand 7,62 mm) | | 
| 1 | U3 | Optokoppler SFH615A | DIP-4_W7.62mm | 
| 1 | U3 | Präzisionssockel 4 Pin (2x 2 Pin, Abstand 7,62 mm) | | 

Bauteile der "dcc_track_UI_TVn"-Platine (Version 1):   
rcc6_dcc_track_UI_TVn_V1_parts   

#### Vorbereitung   
(1) 2x gedrehte, 2-polige Buchsen für die LEDs: Von einer (meist 40-poligen) Buchsenleiste herunterschneiden.  
(2) 2x 4-polige Buchsenleiste für das INA333-Board: Von 8- bzw. 10-poligen Buchsenleisten herunterschneiden.  
(3) 1x 2-polige Stiftleiste von Stiftleiste herunterschneiden (für J3)  
(4) 2x 4-polige Stiftleisten für das INA333-Board: Beiliegende 8-polige Stiftleiste in der Mitte auseinanderschneiden.  
(5) 2x 4-polige Stiftleisten auf der Unterseite des INA333-Boards nach UNTEN anlöten (siehe Bild).  
(6) Bei Print Version 1: Verbindung auf Print `dcc_track_UI_TVn_V1`.  

rcc6_INA333_Board   
_Bild: INA-Board mit angelöteten Stiften_  

#### Best&uuml;ckung   
1. Widerstand R1 (liegend, möglichst flach, 10 k&Omega;)  
2. Widerst&auml;nde Rs2, Rs3 (liegend, möglichst flach, 100 k&Omega;)  
3. Widerstand R5 (liegend, 47 k&Omega;)   
4. Widerstand Rs4 (liegend, 220 k&Omega;)   
5. Diode D3 (BAT48, liegend, auf Polung achten: Kathode bei weißer Linie)   
6. Kondensatoren C1, C2, C4, C7, C8 (1 &micro;F, Raster 2,54 mm)   
7. Buchsenleisten U1 2x 4-Pin (Eventuell INA-Board kurz aufstecken, damit Abstand gut passt.)  
8. gedrehte Buchsen D4, D6 für die LEDs   
9. Fassungen U2 (2x 4 Pin) und U3 (2x 2 Pin, auf Einbaurichtung achten!)   
10. Diode D5 (1N4007, stehend, auf Polung achten: Kathode unten beim Kreis)   
11. Tantal-Elko C3, C5 (10 &micro;F, auf + Polung achten)   
---  
12. Widerst&auml;nde R16, R18 (47 &Omega;)   
13. Widerstand R11 (100 &Omega;)   
14. Widerst&auml;nde R4, R8, R10, R12, R13 (1 k&Omega;)   
15. Widerst&auml;nde ~~R14,~~ R15 (4,7 k&Omega;)   
16. Widerst&auml;nde R2, R6, R7, Rs1 (10 k&Omega;)   
17. Widerstand R3 (22 k&Omega; oder 33 k&Omega;)   
18. Widerst&auml;nde R9, ~~R17~~ (47 k&Omega;)   
19. Elko C6 (Elko 33 &micro;F, auf - Polung achten)   
20. Transistor Q1 (BC337-40)   
21. ~~Transistor Q2 (BC327-40)~~   
22. Stiftleiste 2-polig J3   
23. Diode D1, D2 (SB240, auf Polung achten: Kathode unten beim Kreis)   
---  
24. Wannenstecker 6-polig J5 (auf Polung achten)   
25. Schraubklemme J1, J2 (2-polig)   
26. 10-Gang-Trimmer RV1 (10 k&Omega; stehend, Schraube Richtung U2 LM393)   

#### Print vervollständigen
1. ICs bestücken (LM393, SFH615A, auf richtige Polung achten!)   
2. INA333_Board aufstecken (Trimmer Richtung Print-Rand)   
3. LEDs auf passende Länge kürzen (zB 10 mm) und in die Fassungen stecken (auf richtige Polung achten!)  
rcc4_LED_Polung   

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

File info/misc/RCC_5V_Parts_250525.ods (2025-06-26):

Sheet: Tabelle1
 |  | <Alt>H ... Hide lines <Alt>U ... Unhide lines |  |  |  |  |  | NT | SUB2510L | SUB2510L_NT | SUB2510S | SUB2525 | SUB2525_NT | Shield_5V_DCC_6pol_V3 | Shield_I2C_5V_3V3 | Shield_I2C_5V_3V3_big | uC_small | uC_big | RW_LEER_LED_V1 | RW_5V_2IO_STRG | RW_5V_2IO_LED | 2IO_Add_On | IO2 | IO2+ | RW_5V_1OUT_STRG | RW_5V_1OUT_LED | 1OUT_Add_On | 1OUT | 1OUT+ | RW_5V_DPDT_STRG | RW_5V_DPDT_LED | DPDT_Add_On | DPDT | DPDT+ | CON_2pol_141 | CON_i2c_20mm
PN | Stk | Material | Quelle | Stk/Pkg | €/Pkg | €/Stk | Euro | 0 | 0 | 0 | 0 | 0 | 0 | 0 | 0 | 0 | 0 | 0 | 1 | 0 | 0 | 0 | 0 | 0 | 0 | 0 | 0 | 0 | 0
100 |  | Mechanische Bauteile
101 | 0 | Schraube M2 x 4 mm, Kreuzschlitz, Halbrundkopf, selbstschneidend | Amazon (https://www.amazon.de/dp/B0CR8CRCJS?ref=ppx_yo2ov_dt_b_fed_asin_title&th=1) | 100 | 6,18 | 0,06 | 0,00 |  |  |  |  |  |  |  |  | 4 |  | 4
102 | 0 | Schraube M2 x 10 mm, Kreuzschlitz, Halbrundkopf, selbstschneidend | Amazon (https://www.amazon.de/dp/B0CR8CBRK2?ref=ppx_yo2ov_dt_b_fed_asin_title&th=1) | 100 | 6,54 | 0,07 | 0,00 |  |  |  |  |  |  |  |  |  |  |  |  |  |  | 8 |  | 8 |  |  | 8 |  | 8
103 | 4 | Schraube M2 x 20 mm, Kreuzschlitz, Halbrundkopf | Amazon (https://www.amazon.de/dp/B07QH9KHMG?ref_=ppx_hzsearch_conn_dt_b_fed_asin_title_2) | 100 | 11,09 | 0,11 | 0,44 |  |  |  |  |  |  |  |  |  |  |  | 4 |  |  |  | 4 | 4 |  |  |  | 4 | 4 |  |  |  | 4 | 4
104 | 0 | Schraube M2,5 x 16 mm, Kreuzschlitz PH1, Senkkopf (Flachkopf) | Amazon (https://www.amazon.de/dp/B01LJROU7G?ref=ppx_yo2ov_dt_b_fed_asin_title) | 50 | 8,46 | 0,17 | 0,00 |  | 4 | 4 | 4 | 4 | 4
105 | 0 | Schraube M2,6 x 8 mm, Kreuzschlitz, Halbrundkopf, selbstschneidend | Amazon (https://www.amazon.de/dp/B0CR8C77SK?ref=ppx_yo2ov_dt_b_fed_asin_title&th=1) | 100 | 7,75 | 0,08 | 0,00 |  |  |  |  |  |  |  |  | 4 |  | 4
106 | 4 | Schraube M2,6 x 10 mm, Kreuzschlitz, Halbrundkopf, selbstschneidend | Amazon (https://www.amazon.de/dp/B0CR8C77SK?ref=ppx_yo2ov_dt_b_fed_asin_title&th=1) | 100 | 7,97 | 0,08 | 0,32 |  |  |  |  |  |  |  |  |  |  |  | 4 |  |  |  | 4 | 4 |  |  |  | 4 | 4 |  |  |  | 4 | 4
107 | 0 | Schraube M3 x 35 mm, Kreuzschlitz PH1, Halbrundkopf (Zylinderkopf) | Amazon (https://www.amazon.de/dp/B0BHMPP8M8?ref=ppx_yo2ov_dt_b_fed_asin_title&th=1) | 100 | 9,68 | 0,10 | 0,00 |  | 2 | 2 | 2 | 2 | 2
110 | 4 | Sechskantmutter M2 x 0,4 mm | Amazon (https://www.amazon.de/sourcing-map-Kohlenstoff-Hexagonal-Silbert%C3%B6ne/dp/B07J3CNWNH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) | 200 | 7,25 | 0,04 | 0,15 |  |  |  |  |  |  |  |  | 4 |  | 4 | 4 |  |  |  | 4 | 4 |  |  |  | 4 | 4 |  |  |  | 4 | 4
111 | 0 | Sechskantmutter M2,5 x 0,45 mm | Amazon (https://www.amazon.de/dp/B07JHFHSF2?ref=ppx_yo2ov_dt_b_fed_asin_title) | 200 | 6,74 | 0,03 | 0,00 |  | 4 | 4 | 4 | 4 | 4
112 | 0 | Sechskantmutter M3 | Amazon (https://www.amazon.de/Edelstahl-4032-Sechskant-St%C3%BCck-Sechskantmuttern/dp/B07ZB661WG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) | 100 | 8,56 | 0,09 | 0,00 |  | 2 | 2 | 2 | 2 | 2
113 | 4 | Abstandhalter M2 x 10 + 3 mm, Sechskant, Messing, männlich-weiblich | Amazon (https://www.amazon.de/gp/product/B0BXDHL2YP/ref=ppx_yo_dt_b_search_asin_title?ie=UTF8&psc=1) | 60 | 12,91 | 0,22 | 0,86 |  |  |  |  |  |  |  |  | 4 |  | 4 | 4 |  |  |  | 4 | 4 |  |  |  | 4 | 4 |  |  |  | 4 | 4
114 | 0 | Schrumpfschlauch 1/16inch (1mm) Schrumpfverhältnis 2:1 | Amazon (https://www.amazon.de/dp/B08R22XP69?ref=ppx_yo2ov_dt_b_fed_asin_title) | 6 | 6,59 | 1,10 | 0,00 |  |  |  |  |  |  |  |  |  |  |  |  |  | 0,2 |  | 0,2 | 0,2 |  | 0,12 |  | 0,12 | 0,12
115 | 0 | Schrumpfschlauch 3/32inch (2mm) Schrumpfverhältnis 2:1 | Amazon (https://www.amazon.de/dp/B08R22XP69?ref=ppx_yo2ov_dt_b_fed_asin_title) | 6 | 6,89 | 1,15 | 0,00 |  |  |  |  |  |  | 0,03 |  |  | 0,03 | 0,03
116 | 0 | LED-Fassung 3mm, Chrom-Messing, hervorstehende Lünette, 6 mm Durchmesser, Schraubplattenmontage | AliExpress Daier Store (https://de.aliexpress.com/item/1005007180033606.html) | 20 | 12,68 | 0,63 | 0,00 |  |  |  |  |  |  |  |  |  |  |  |  |  | 5 |  | 5 | 5 |  | 3 |  | 3 | 3
120 | 0 | Knopf für Taster/Schalter 8x8mm, Länge 10mm, 7 verschiedene Farben | AliExpress Ali_CanHui Store (https://de.aliexpress.com/item/1005001524633998.html) | 70 | 1,92 | 0,03 | 0,00 |  |  |  |  |  |  |  |  |  |  |  |  |  | 2 |  | 2 | 2 |  | 1 |  | 1 | 1
121 | 0 | Knopf für Taster/Schalter 8x8mm, Länge 7mm, weiß | AliExpress TEJIATE Store (https://de.aliexpress.com/item/4000504035520.html) | 100 | 2,08 | 0,02 | 0,00 |  |  |  |  |  |  |  |  |  |  |  |  |  |  |  |  |  |  | 1 |  | 1 | 1
122 | 0 | Knopf für Taster/Schalter 8x8mm, Länge 7mm, gelb | AliExpress Century Mingsheng Store (https://de.aliexpress.com/item/1005005802857495.html) | 50 | 3,25 | 0,07 | 0,00
123 | 0 | Knopf für Taster/Schalter 8x8mm, Länge 7mm, grün | AliExpress TEJIATE Store (https://de.aliexpress.com/item/4000504035520.html) | 100 | 2,10 | 0,02 | 0,00 |  |  |  |  |  |  |  |  |  |  |  |  |  | 1 |  | 1 | 1
124 | 0 | Knopf für Taster/Schalter 8x8mm, Länge 7mm, rot | AliExpress TEJIATE Store (https://de.aliexpress.com/item/4000504035520.html) | 100 | 2,06 | 0,02 | 0,00 |  |  |  |  |  |  |  |  |  |  |  |  |  | 1 |  | 1 | 1
125 | 0 | Knopf für Taster/Schalter 8x8mm, Länge 7mm, blau | AliExpress TEJIATE Store (https://de.aliexpress.com/item/4000504035520.html) | 100 | 2,10 | 0,02 | 0,00
126 | 0 | Knopf für Taster/Schalter 8x8mm, Länge 7mm, schwarz | AliExpress TEJIATE Store (https://de.aliexpress.com/item/4000504035520.html) | 100 | 1,99 | 0,02 | 0,00
 | 0 |  | X |  |  | 0,00 | 0,00
 | 0 |  | X |  |  | 0,00 | 0,00
 | 0 |  | X |  |  | 0,00 | 0,00
200 |  | Elektro-mechanisch
201 | 0 | Stiftleiste 1x8-polig, gerade | AliExpress (https://de.aliexpress.com/item/4000988113226.html) | 30 | 2,15 | 0,07 | 0,00 | 1 |  | 1 |  |  |  |  | 2 | 4 | 2 | 4 |  | 2 |  | 1 | 2 | 3 | 2 |  | 1 | 2 | 3
202 | 0 | Stiftleiste 1x40-polig, rechtwinklig abgewinkelt (90°) 2,54 mm, R1 Type B6, extra langer Stift | AliExpress E-Simpo Store (https://de.aliexpress.com/item/32887929634.html) | 20 | 6,18 | 0,31 | 0,00 |  |  |  |  |  |  | 1 |  |  | 1 | 1
203 | 2 | Buchsenleiste 1x8-polig, kurze Anschlüsse, 2,54mm | AliExpress TLZWLA Official Store (https://de.aliexpress.com/item/4001198553093.html) | 100 | 5,99 | 0,06 | 0,12 |  |  |  |  |  |  |  | 1 | 1 | 1 | 1 | 2 |  |  |  | 2 | 2 |  |  |  | 2 | 2 |  |  |  | 2 | 2
204 | 0 | Buchsenleiste 1x8-polig, lange Anschlüsse (11 mm), 2,54mm | AliExpress Supplier of electronic components (https://de.aliexpress.com/item/4000287613735.html) | 10 | 1,93 | 0,19 | 0,00 | 3 |  | 3 |  |  |  | 3 | 2 |  | 5 | 3 |  |  | 2 |  | 2 | 2 |  | 2 |  | 2 | 2
205 | 0 | Buchsenleiste 1x10-polig, kurze Anschlüsse, 2,54mm | AliExpress Z-L Store (https://de.aliexpress.com/item/1005005488898046.html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) | 10 | 1,99 | 0,20 | 0,00
206 | 0 | Buchsenleiste 1x40-polig, gedrehte Kontakte, 2,54mm, vergoldet (single row female round hole) | AliExpress Sincere Company Store (https://de.aliexpress.com/item/1005006755553448.html) | 5 | 7,91 | 1,58 | 0,00 |  |  |  |  |  |  |  |  |  |  |  |  |  | 0,3 |  | 0,3 | 0,3 |  | 0,15 |  | 0,15 | 0,15
210 | 0 | Wannenstecker 6-polig, stehend | AliExpress Quality module supplier Store (https://de.aliexpress.com/item/1005006804603387.html) | 10 | 1,88 | 0,19 | 0,00 | 2 |  | 2 |  |  |  |  |  |  |  |  |  | 2 |  | 1 | 2 | 3 | 2 |  | 1 | 2 | 3
211 | 0 | Wannenstecker 6-polig, 90° abgewinkelt | AliExpress Danteqi Connectors Store (https://de.aliexpress.com/item/1005007473702559.html) | 10 | 2,93 | 0,29 | 0,00 |  |  |  |  |  |  | 1 |  |  | 1 | 1
212 | 0 | Wannenstecker 10-polig, stehend | AliExpress Quality module supplier Store (https://de.aliexpress.com/item/1005006804603387.html) | 10 | 1,90 | 0,19 | 0,00 |  |  |  |  |  |  |  |  |  |  |  |  | 1 |  | 1 | 1 | 2 | 1 | 1 | 1 | 1 | 2
213 | 0 | Wannenstecker 10-polig, 90° abgewinkelt | AliExpress Danteqi Connectors Store (https://de.aliexpress.com/item/1005007473702559.html) | 10 | 0,83 | 0,08 | 0,00
214 | 0 | IDC Buchsen-Stecker für Flachbandkabel 6-polig | AliExpress All Electr Connection Store (https://de.aliexpress.com/item/1005002804645942.html) | 10 | 2,89 | 0,29 | 0,00 |  |  |  |  |  |  |  |  |  |  |  |  |  |  | 2 |  | 2 |  |  | 2
215 | 0 | IDC Buchsen-Stecker für Flachbandkabel 10-polig | AliExpress All Electr Connection Store (https://de.aliexpress.com/item/1005002804645942.html) | 10 | 2,78 | 0,28 | 0,00 |  |  |  |  |  |  |  |  |  |  |  |  |  |  | 2 |  | 2 |  |  | 2
220 | 0 | Sub-D-Stecker 25-polig (DB25_Plug) (DR25, Male) | AliExpress Shop5585334 Store (https://de.aliexpress.com/item/1005003119025143.html) | 5 | 4,78 | 0,96 | 0,00 |  | 1 | 1 | 1 | 2 | 2
221 | 0 | Schraubklemme 2-polig, schwarz | AliExpress GZ BINXINRUI Store (https://de.aliexpress.com/item/1005007145396958.html) | 50 | 12,01 | 0,24 | 0,00 |  | 5 | 5 | 2 | 3 | 3 |  |  |  |  |  |  |  |  | 3 |  | 3
222 | 0 | Schraubklemme 2-polig, grün | AliExpress GZ BINXINRUI Store (https://de.aliexpress.com/item/1005007145396958.html) | 50 | 12,21 | 0,24 | 0,00 |  | 2 | 2 | 2
223 | 0 | Schraubklemme 2-polig, rot | AliExpress GZ BINXINRUI Store (https://de.aliexpress.com/item/1005007145396958.html) | 50 | 12,01 | 0,24 | 0,00 |  | 1 | 1 | 1
224 | 0 | Schraubklemme 2-polig, blau | AliExpress GZ BINXINRUI Store (https://de.aliexpress.com/item/1005007145396958.html) | 50 | 12,01 | 0,24 | 0,00 |  | 1 | 1 |  | 1 | 1
225 | 0 | Schraubklemme 3-polig, blau | AliExpress GZ BINXINRUI Store (https://de.aliexpress.com/item/1005007145396958.html) | 50 | 14,90 | 0,30 | 0,00
226 | 0 | Schraubklemme 3-polig, rot | AliExpress GZ BINXINRUI Store (https://de.aliexpress.com/item/1005007145396958.html) | 50 | 14,37 | 0,29 | 0,00 |  |  |  |  |  |  |  |  |  |  |  |  |  |  |  |  |  |  |  | 1
230 | 0 | Wasserdichte Drucktaster Edelstahl Taster EIN Aus 12mm 2A/12V/24V/125V/250V mit Draht (Hervorstehend) | Amazon (https://www.amazon.de/dp/B08L49F7DV?ref=ppx_yo2ov_dt_b_fed_asin_title&th=1) | 5 | 8,05 | 1,61 | 0,00 |  |  |  |  |  |  | 1 |  |  | 1 | 1
231 | 0 | Microtaster 2x Um (DPDT), Unlock 8x8mm | AliExpress BXV_computer chipset_Store (https://de.aliexpress.com/item/1005006962539948.html) | 10 | 5,77 | 0,58 | 0,00 |  |  |  |  |  |  |  |  |  |  |  |  |  |  |  |  |  |  | 1 |  | 1 | 1
232 | 0 | Microschalter 2x Um (DPDT), Locking 8x8mm | AliExpress BXV_computer chipset_Store (https://de.aliexpress.com/item/1005006962539948.html) | 10 | 5,61 | 0,56 | 0,00 |  |  |  |  |  |  |  |  |  |  |  |  |  | 2 |  | 2 | 2
240 | 0 | IC-Fassung 4-polig, IC socket with turned contacts 4-pin | AliExpress BOOHLG Official Store (https://de.aliexpress.com/item/1005003652148420.html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) | 50 | 4,55 | 0,09 | 0,00 |  |  |  |  |  |  |  |  |  |  |  |  | 1 |  |  | 1 | 1 | 1 |  |  | 1 | 1
241 | 0 | IC-Fassung 8-polig, IC socket with turned contacts 8-pin | AliExpress Supplier of components Store (https://de.aliexpress.com/item/1005007246586839.html) | 10 | 1,89 | 0,19 | 0,00 |  |  |  |  |  |  | 1 |  |  | 1 | 1
242 | 0 | Jumper 2-polig, 2,54 mm, oben offen | Amazon (https://www.amazon.de/CQRobot-Jumper-Kappe-Stiftleisten-Kurzschluss-Anschluss-Schwarz/dp/B0B5LGCMDT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) | 200 | 10,07 | 0,05 | 0,00
 | 0 |  | X |  |  | 0,00 | 0,00
 | 0 |  | X |  |  | 0,00 | 0,00
300 |  | Elektrik
301 | 0 | Flachbandkabel 6-polig | AliExpress (https://de.aliexpress.com/item/1005005382567357.html?productId=1005005382567357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) | 5 | 4,68 | 0,94 | 0,00 |  |  |  |  |  |  |  |  |  |  |  |  |  |  | 0,3 |  | 0,3 |  |  | 0,3 |  | 0,3
302 | 0 | Flachbandkabel 10-polig | AliExpress (https://de.aliexpress.com/item/1005005382567357.html?productId=1005005382567357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) | 5 | 5,68 | 1,14 | 0,00 |  |  |  |  |  |  |  |  |  |  |  |  |  |  | 0,1 |  | 0,1 |  |  | 0,1 |  | 0,1
303 | 0 | Drähte Jumper Wire Cable 10 cm Female-Female | Amazon (https://www.amazon.de/dp/B072JT6BCN?ref=ppx_yo2ov_dt_b_fed_asin_title&th=1) | 120 | 7,04 | 0,06 | 0,00
304 | 0 | Drähte Jumper Wire Cable 30 cm Male-Female | AliExpress Shop1103694164 Store (https://de.aliexpress.com/item/1005007032334210.html) | 400 | 5,40 | 0,01 | 0,00 |  |  |  |  |  |  |  | 4 |  | 4
305 | 0 | Drähte Jumper Wire Cable 30 cm Female-Female | AliExpress Shop1103694164 Store (https://de.aliexpress.com/item/1005007032334210.html) | 400 | 5,52 | 0,01 | 0,00 |  |  |  |  |  |  |  | 4 | 4 | 4 | 4
 | 0 |  | X |  |  | 0,00 | 0,00
 | 0 |  | X |  |  | 0,00 | 0,00
400 |  | Elektronik
401 | 0 | ESP32 D1 mini mit CH9102X drive Type-C | AliExpress SAMIORE Choice Store (https://de.aliexpress.com/item/1005005972627549.html) | 1 | 12,05 | 12,05 | 0,00
402 | 0 | OLED-Display 1,54 Zoll, I2C 4 Pin weiß | AliExpress All-goods-are-freeshipping Store (https://de.aliexpress.com/item/1005008521802913.html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) | 1 | 4,99 | 4,99 | 0,00 |  |  |  |  |  |  |  | 1 | 1 | 1 | 1
403 | 0 | Relais HFD4-3 DIP 3V | AliExpress Source Of Information Store (https://de.aliexpress.com/item/1005005783041160.html) | 20 | 22,91 | 1,15 | 0,00 |  |  |  |  |  |  |  |  |  |  |  |  | 1 |  |  | 1 | 1 | 1 |  |  | 1 | 1
404 | 0 | Relais HFD4-5 DIP 5V (oder AXICOM IM03TS 5VDC) | AliExpress HangGuo Store (https://de.aliexpress.com/item/1005007261952244.html) | 5 | 6,84 | 1,37 | 0,00
405 | 0 | Optokoppler SFH 615A-4 | AliExpress shenzhenYida Store (https://de.aliexpress.com/item/1005002283822668.html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) | 10 | 2,04 | 0,20 | 0,00 |  |  |  |  |  |  |  |  |  |  |  |  | 1 |  |  | 1 | 1 | 1 |  |  | 1 | 1
406 | 0 | Optokoppler 6N137 | AliExpress China IC Sales Store (https://de.aliexpress.com/item/1005002002451701.html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) | 10 | 2,20 | 0,22 | 0,00 |  |  |  |  |  |  | 1 |  |  | 1 | 1
407 | 0 | Transistor BC327-40 PNP | Reichelt (https://www.reichelt.at/at/de/shop/produkt/bipolartransistor_pnp_45v_0_5a_0_625w_to-92-219124) | 1 | 0,04 | 0,04 | 0,00 |  |  |  |  |  |  |  |  |  |  |  |  | 1 |  |  | 1 | 1 | 1 |  |  | 1 | 1
408 | 0 | Transistor BC337-40 NPN | Reichelt (https://www.reichelt.at/at/de/shop/produkt/bipolartransistor_npn_45v_0_8a_0_625w_to-92-219126) | 1 | 0,04 | 0,04 | 0,00 |  |  |  |  |  |  |  |  |  |  |  |  |  | 1 |  | 1 | 1 |  | 1 |  | 1 | 1
409 | 0 | LED 3mm, 2mA, bedrahtet, rot, 5mcd, 60° | Reichelt (https://www.reichelt.com/at/de/shop/produkt/led_3_mm_bedrahtet_rot_5_mcd_60_-21626?nbc=1) | 1 | 0,15 | 0,15 | 0,00 |  |  |  |  |  |  |  |  |  |  |  |  |  | 1 |  | 1 | 1 |  | 1 |  | 1 | 1
410 | 0 | LED 3mm, 2mA, bedrahtet, gelb, 3,2mcd, 60° | Reichelt (https://www.reichelt.com/at/de/shop/produkt/led_3_mm_bedrahtet_gelb_3_2_mcd_60_-21628) | 1 | 0,15 | 0,15 | 0,00 |  |  |  |  |  |  |  |  |  |  |  |  |  | 3 |  | 3 | 3 |  | 1 |  | 1 | 1
411 | 0 | LED 3mm, 2mA, bedrahtet, grün, 3,2mcd, 60° | Reichelt (https://www.reichelt.at/at/de/shop/produkt/led_3_mm_bedrahtet_gruen_3_2_mcd_60_-21624?nbc=1) | 1 | 0,15 | 0,15 | 0,00 |  |  |  |  |  |  |  |  |  |  |  |  |  | 1 |  | 1 | 1 |  | 1 |  | 1 | 1
412 | 0 | Diode 1N4148 | AliExpress DSSRQI Official Store (https://de.aliexpress.com/item/4000142272546.html) | 100 | 1,74 | 0,02 | 0,00 |  |  |  |  |  |  | 1 |  |  | 1 | 1 |  | 3 |  |  | 3 | 3 | 4 |  |  | 4 | 4
413 | 0 | Diode 1N4007 | AliExpress IBUW Electronic Store (https://de.aliexpress.com/item/1005005707666232.html?scm_id=1007.13440.311564.0&scm-url=1007.13440.311564.0) | 100 | 1,85 | 0,02 | 0,00 | 1 |  | 1 |  |  | 1 |  |  |  |  |  |  | 1 |  |  | 1 | 1 | 1 |  |  | 1 | 1
220 | 0 | Elko radial, 1000 uF, 35V, 10x20mm | AliExpress Xiazhi Store | 10 | 2,23 | 0,22 | 0,00 | 1 |  | 1 |  |  | 1
221 | 0 | Elko radial, 33 uF, 35 V, 8x5mm | AliExpress JXNSGUW Store (https://de.aliexpress.com/item/1005003108572892.html) | 20 | 10,17 | 0,51 | 0,00 |  |  |  |  |  |  |  |  |  |  |  |  | 1 |  |  | 1 | 1 | 1 |  |  | 1 | 1
222 | 0 | Kondensator 100nF, 100 V, RM 5mm | AliExpress Microelectronics Technology (https://de.aliexpress.com/item/32904550088.html) | 40 | 2,22 | 0,06 | 0,00 |  |  |  |  |  |  |  |  |  |  |  |  | 1 |  |  | 1 | 1 | 1 |  |  | 1 | 1
223 | 0 | Kondensator 100 nF (104), 50 V, 2,54 mm (Vielschicht-Kerko) | AliExpress Manufacturer of Module Store (https://de.aliexpress.com/item/32865098104.html) | 50 | 2,17 | 0,04 | 0,00 |  |  |  |  |  |  | 1 |  |  | 1 | 1
224 | 0 | Kondensator 10 nF (103), 50 V, 2,54 mm | AliExpress Manufacturer of Module Store (https://de.aliexpress.com/item/32865098104.html) | 50 | 2,15 | 0,04 | 0,00
225 | 0 | Kondensator 1 nF (102), 50 V, 2,54 mm | AliExpress Manufacturer of Module Store (https://de.aliexpress.com/item/32865098104.html) | 50 | 2,25 | 0,05 | 0,00 |  |  |  |  |  |  | 1 |  |  | 1 | 1
230 | 0 | Leistungswiderstand 4,7Ω/5W | Reichelt (https://www.reichelt.com/at/de/shop/produkt/drahtwiderstand_axial_5_w_4_7_ohm_10_-2623?nbc=1) | 1 | 0,35 | 0,35 | 0,00 | 1 |  | 1 |  |  | 1
231 | 0 | Widerstand 47 Ohm, Kohleschicht, 0207, 250 mW, 5% | Reichelt (https://www.reichelt.de/de/de/shop/produkt/widerstand_kohleschicht_47_ohm_0207_250_mw_5_-1431#) | 100 | 2,10 | 0,02 | 0,00 |  |  |  |  |  |  |  |  |  |  |  |  |  | 1 |  | 1 | 1 |  | 2 |  | 2 | 2
232 | 0 | Widerstand 100 Ohm, Kohleschicht, 0207, 250 mW, 5% | Reichelt (https://www.reichelt.de/de/de/shop/produkt/widerstand_kohleschicht_100_ohm_0207_250_mw_5_-1336) | 100 | 2,10 | 0,02 | 0,00 |  |  |  |  |  |  |  |  |  |  |  |  | 1 |  |  | 1 | 1 | 1 |  |  | 1 | 1
233 | 0 | Widerstand 1 kOhm, Kohleschicht, 0207, 250 mW, 5% | Neuhold (https://www.neuhold-elektronik.at/widerstaende-1-4w/1-ko-widerstand-1-4-w-100-stueck) | 100 | 1,20 | 0,01 | 0,00 |  |  |  |  |  |  | 2 |  |  | 2 | 2 |  | 1 | 5 |  | 6 | 6 | 1 | 3 |  | 4 | 4
234 | 0 | Widerstand 4,7 kOhm, Kohleschicht, 0207, 250 mW, 5% | Neuhold (https://www.neuhold-elektronik.at/widerstaende-1-4w/4-7-ko-widerstand-1-4-w-100-stueck) | 100 | 1,20 | 0,01 | 0,00 |  |  |  |  |  |  |  |  |  |  |  |  | 1 |  |  | 1 | 1 | 2 |  |  | 2 | 2
235 | 0 | Widerstand 10 kOhm, Kohleschicht, 0207, 250 mW, 5% | Neuhold (https://www.neuhold-elektronik.at/widerstaende-1-4w/10-ko-widerstand-1-4-w-100-stueck) | 100 | 1,20 | 0,01 | 0,00 |  |  |  |  |  |  | 2 |  |  | 2 | 2 |  | 1 | 1 |  | 2 | 2 | 1 | 1 |  | 2 | 2
236 | 0 | Widerstand 47 kOhm, Kohleschicht, 0207, 250 mW, 5% | Neuhold (https://www.neuhold-elektronik.at/widerstaende-1-4w/47-ko-widerstand-1-4-w-100-stueck) | 100 | 1,20 | 0,01 | 0,00
237 | 0 | Widerstand 100 kOhm, Kohleschicht, 0207, 250 mW, 5% | Neuhold (https://www.neuhold-elektronik.at/widerstaende-1-4w/100-ko-widerstand-1-4-w-100-stueck) | 100 | 1,20 | 0,01 | 0,00 |  |  |  |  |  |  |  |  |  |  |  |  | 1 | 1 |  | 2 | 2 | 1 | 1 |  | 2 | 2
 | 0 |  | X |  |  | 0,00 | 0,00
 | 0 |  | X |  |  | 0,00 | 0,00
500 |  | Platinen
501 | 0 | Leiterplatte: AC_5V_6pol_DCC | PCBWay | 10 | 9,50 | 0,95 | 0,00 | 1 |  | 1 |  |  | 1
502 | 0 | Leiterplatte: RW_5V_SUB25_10 | PCBWay | 10 | 9,50 | 0,95 | 0,00 |  | 1 | 1
503 | 0 | Leiterplatte: CON_SubD_Screw10 | PCBWay | 10 | 9,50 | 0,95 | 0,00 |  |  |  | 1
504 | 0 | Leiterplatte: RW_5V_2SUB25 | PCBWay | 10 | 9,50 | 0,95 | 0,00 |  |  |  |  | 1 | 1
505 | 0 | Leiterplatte: Shield_5V_DCC_6pol_V3 | PCBWay | 10 | 9,50 | 0,95 | 0,00 |  |  |  |  |  |  | 1 |  |  | 1 | 1
506 | 0 | Leiterplatte: Shield_I2C_5V_3V3_V2 | PCBWay | 10 | 9,50 | 0,95 | 0,00 |  |  |  |  |  |  |  | 1 |  | 1
507 | 0 | Leiterplatte: Shield_I2C_5V_3V3_big_V2 | PCBWay | 10 | 9,50 | 0,95 | 0,00 |  |  |  |  |  |  |  |  | 1 |  | 1
508 | 1 | Leiterplatte: RW_LEER_LED_V1 | PCBWay | 10 | 9,50 | 0,95 | 0,95 |  |  |  |  |  |  |  |  |  |  |  | 1 |  |  |  | 1 | 1 |  |  |  | 1 | 1 |  |  |  | 1 | 1
509 | 0 | Leiterplatte: RW_5V_W2_STRG | PCBWay | 10 | 9,50 | 0,95 | 0,00
510 | 0 | Leiterplatte: RW_5V_W2_LED | PCBWay | 10 | 9,50 | 0,95 | 0,00
511 | 0 | Leiterplatte: CON_6pol_3_V2 | PCBWay | 10 | 9,50 | 0,95 | 0,00 |  |  |  |  |  |  |  |  |  |  |  |  |  |  |  |  |  |  |  | 1 |  | 1
512 | 0 | Leiterplatte: CON_10pol_2x4_V1 | PCBWay | 10 | 9,50 | 0,95 | 0,00 |  |  |  |  |  |  |  |  |  |  |  |  |  |  | 1 |  | 1 |  |  | 1 |  | 1
513 | 0 | Leiterplatte: RW_5V_W3_STRG | PCBWay | 10 | 9,50 | 0,95 | 0,00
514 | 0 | Leiterplatte: RW_5V_W3_LED | PCBWay | 10 | 9,50 | 0,95 | 0,00
515 | 0 | Leiterplatte: CON_6pol_6_V2 | PCBWay | 10 | 9,50 | 0,95 | 0,00
516 | 0 | Leiterplatte: RW_5V_2IO_STRG | PCBWay | 10 | 9,50 | 0,95 | 0,00 |  |  |  |  |  |  |  |  |  |  |  |  | 1 |  |  | 1 | 1
517 | 0 | Leiterplatte: RW_5V_2IO_LED | PCBWay | 10 | 9,50 | 0,95 | 0,00 |  |  |  |  |  |  |  |  |  |  |  |  |  | 1 |  | 1 | 1
518 | 0 | Leiterplatte: CON_1xIO_V2 | PCBWay | 10 | 9,50 | 0,95 | 0,00 |  |  |  |  |  |  |  |  |  |  |  |  |  |  | 1 |  | 1
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

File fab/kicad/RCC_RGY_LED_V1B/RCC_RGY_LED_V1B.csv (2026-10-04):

ID | Bezeichner | Footprint | Stückzahl | Bezeichnung | Anbieter und Referenz
1 | C1 | C_L4.3mm_D2.8mm_P5.08mm_kh | 1 | 1u
2 | D1, D2, D3 | LED_D5.0mm-3 | 3 | LED_Dual_AKA
3 | D4 | D_DO-35_P3.81mm_Vertical_AnodeUp_kh | 1 | 1N4148
4 | D5 | D_DO-35_P2.0mm_Vertical_AnodeUp_kh | 1 | 1N4148
5 | D6, D7 | D_DO-35_SOD27_P2.54mm_Vertical_AnodeUp_kh | 2 | BAT48
6 | J1, J2 | PinSocket_1x08_P2.54mm_Vertical_11mm_kh | 2 | Conn_01x08_Pin
7 | Q1, Q2, Q3, Q4, Q5 | TO-92_Inline_Wide_custom | 5 | BC337
8 | R1 | R_Axial_DIN0204_L3.6mm_D1.6mm_P2.54mm_Vertical_kh | 1 | 680
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

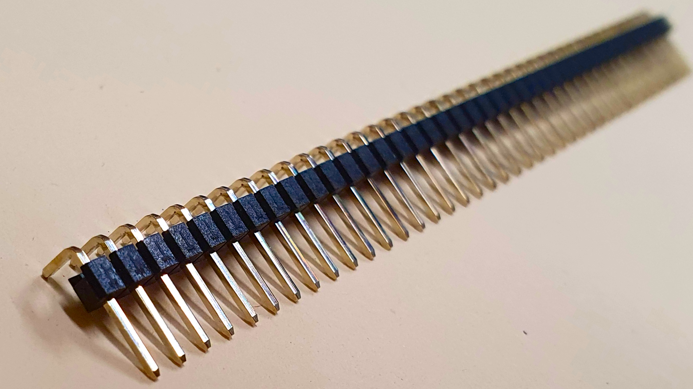
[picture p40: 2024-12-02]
images/parts/o_pin_header_90.png

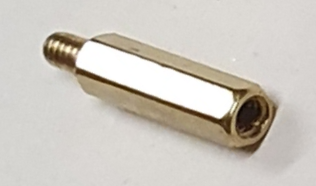
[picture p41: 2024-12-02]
images/parts/o_spacers_M2x10.png

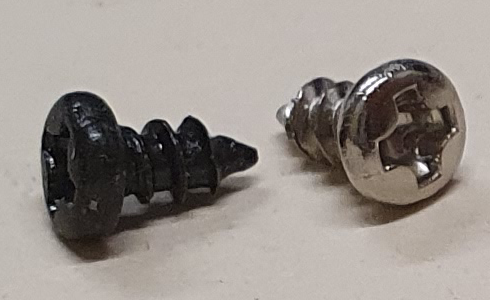
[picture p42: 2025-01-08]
images/parts/300_self-drilling_screw_M2x4.png

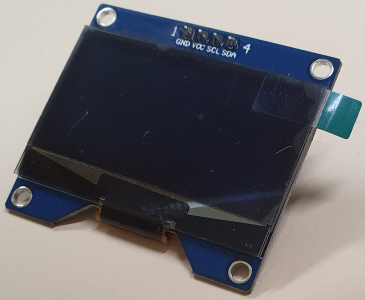
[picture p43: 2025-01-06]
images/parts/300_oled154.png

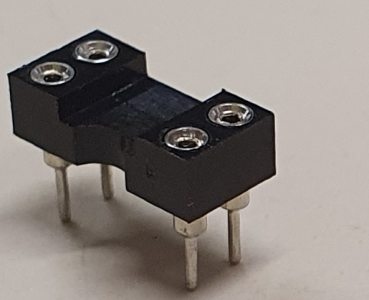
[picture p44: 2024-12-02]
images/parts/300_IC4.png

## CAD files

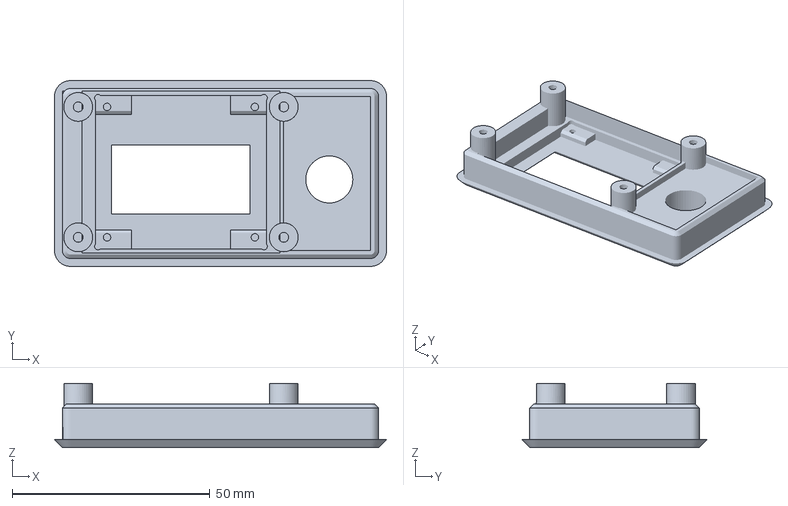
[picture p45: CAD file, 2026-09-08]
fab/3d/3mf/OLED-Mount_250209.3mf
84.0 x 47.0 x 16.2 mm

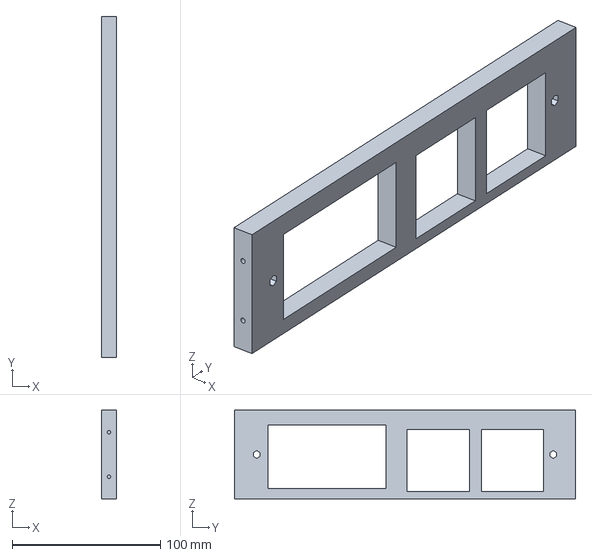
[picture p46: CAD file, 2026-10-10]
fab/3d/Rahmen_Front_S_Oled_34_230mm_260906.FCStd
10.0 x 230.0 x 60.0 mm

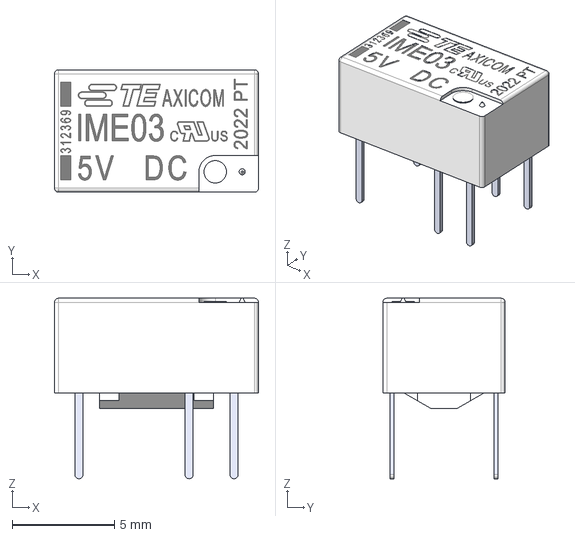
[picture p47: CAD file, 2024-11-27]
fab/kicad/3D/Relays/IME03TS Relay (TE Connectivity).step
10.0 x 6.00 x 8.85 mm

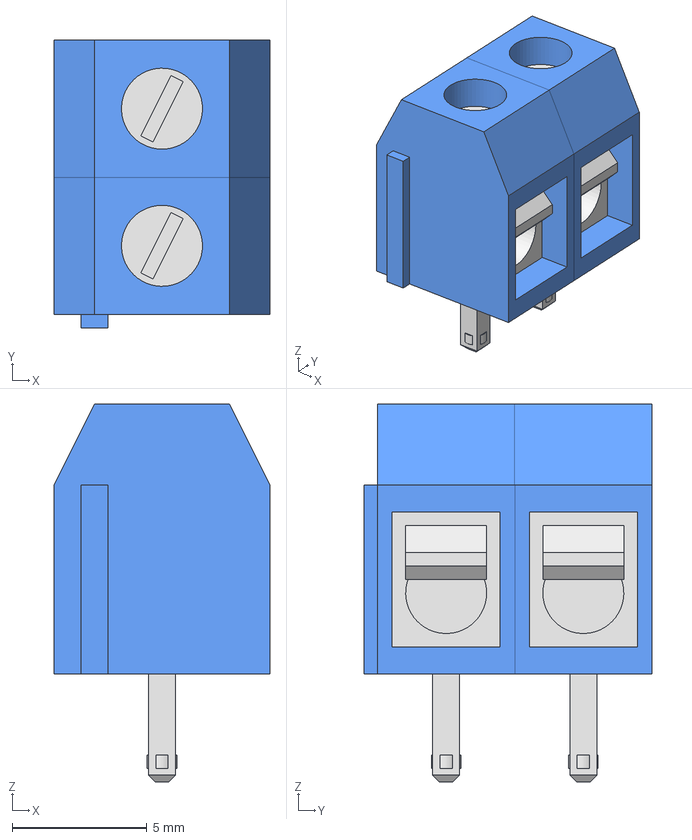
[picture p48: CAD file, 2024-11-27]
fab/kicad/3D/Schraubklemme_Blau_300V_16A_2P.stp
8.00 x 10.7 x 14.0 mm
Schraubklemme_Blau_300V_16A x 2

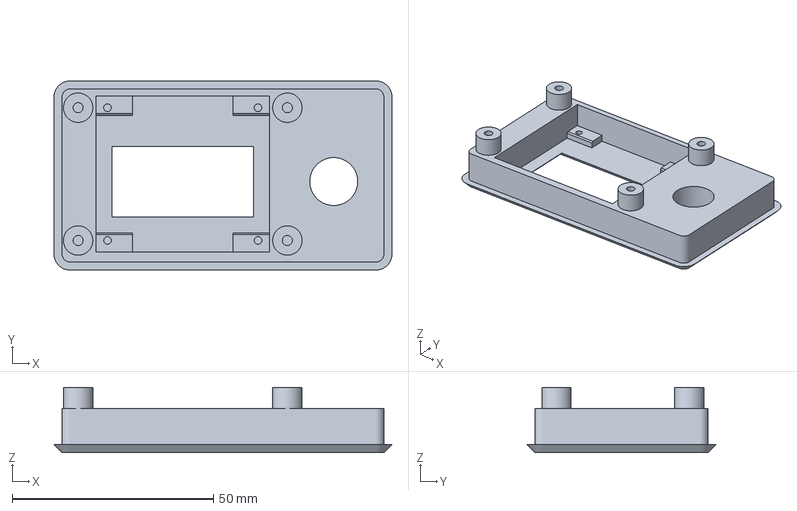
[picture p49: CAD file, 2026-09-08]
fab/3d/3mf/OLED_Mount_prusa_260313.3mf
84.0 x 47.0 x 16.2 mm

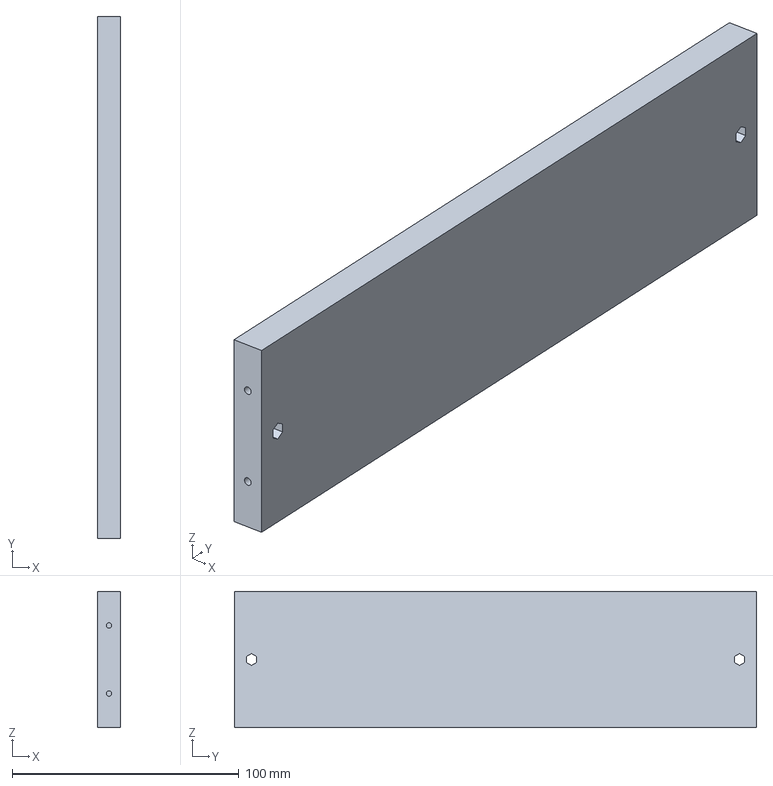
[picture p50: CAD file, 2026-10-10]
fab/3d/Rahmen_Back_N__230mm_261008.FCStd
10.0 x 230.0 x 60.0 mm

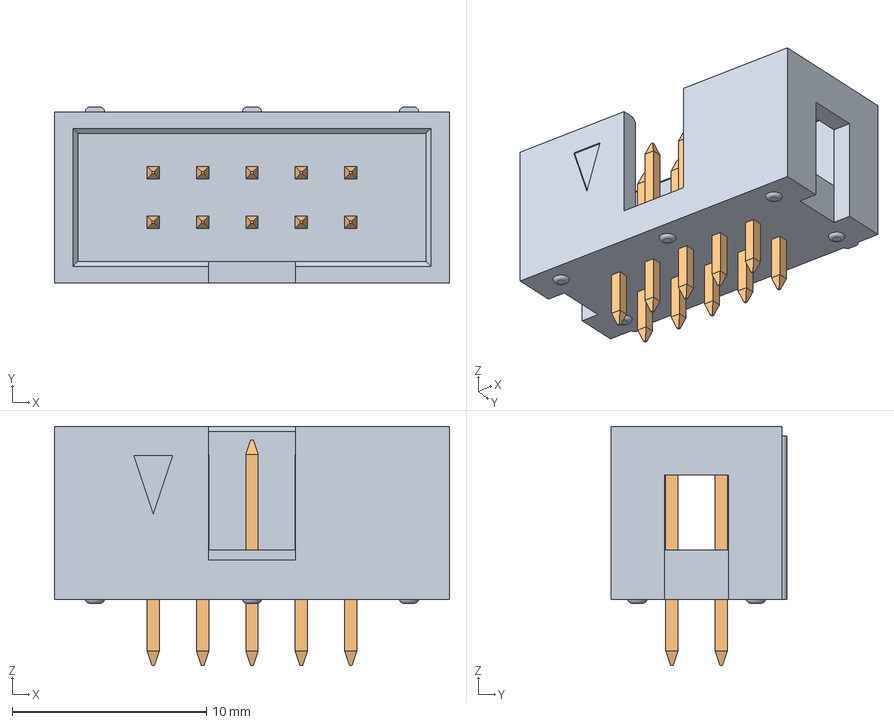
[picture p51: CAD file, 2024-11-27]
fab/kicad/3D/Box_02x05_P2.54_Vertikal.step
20.3 x 9.05 x 12.3 mm

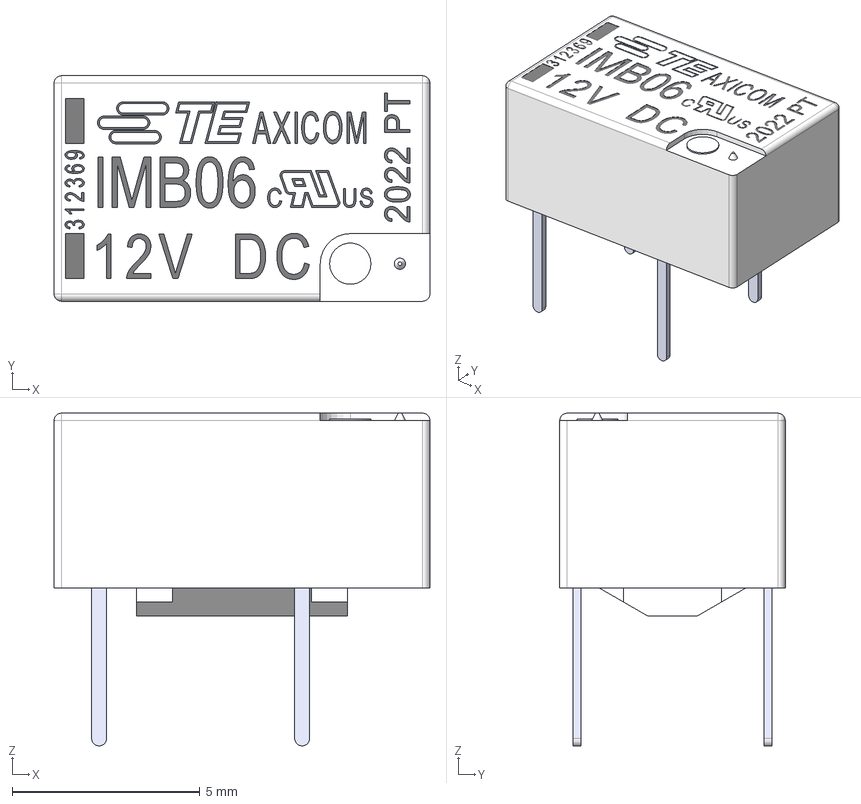
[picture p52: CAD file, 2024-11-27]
fab/kicad/3D/Relays/IMB06CTS Relay (TE Connectivity).step
10.0 x 6.00 x 8.85 mm

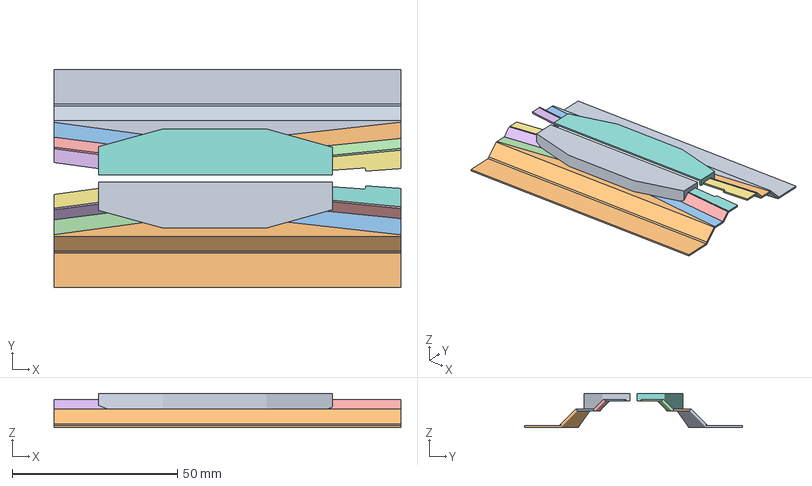
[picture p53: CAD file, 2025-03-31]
fab/3d/3mf/Weichenabdeckung_3Weg_beide_v2.3mf
105.0 x 66.0 x 10.4 mm
Körper1
Körper17
Körper18
Körper19
Körper20
Körper21
Körper22
Körper23
Körper25
Körper43
Körper44
Körper45
Körper46
Körper47
Körper48
Körper49
Körper50
Körper51

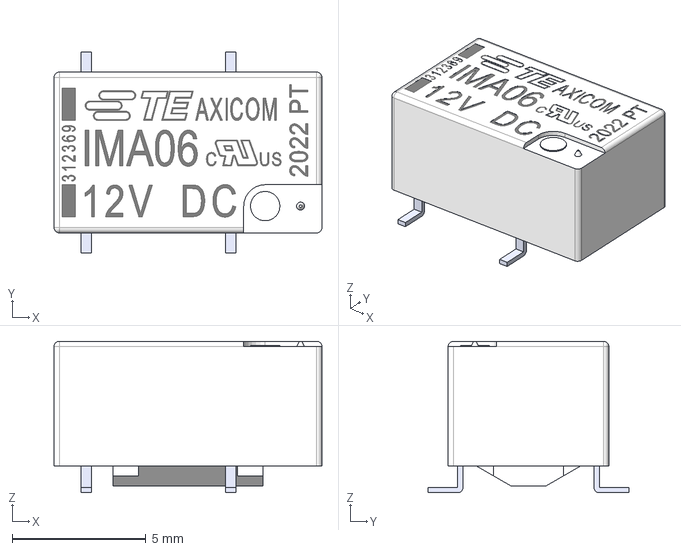
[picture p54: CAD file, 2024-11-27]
fab/kicad/3D/Relays/IMA06CGR Relay (TE Connectivity).step
10.0 x 7.50 x 5.65 mm

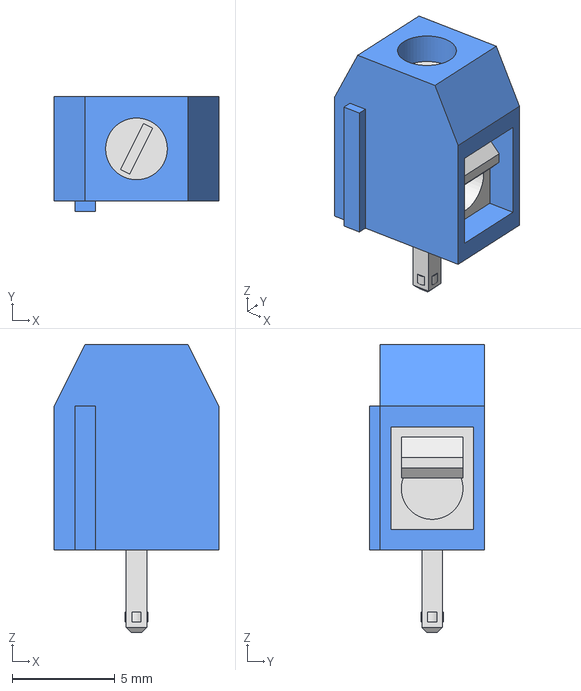
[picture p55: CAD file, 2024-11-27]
fab/kicad/3D/Schraubklemme_Blau_300V_16A.stp
8.00 x 5.58 x 14.0 mm

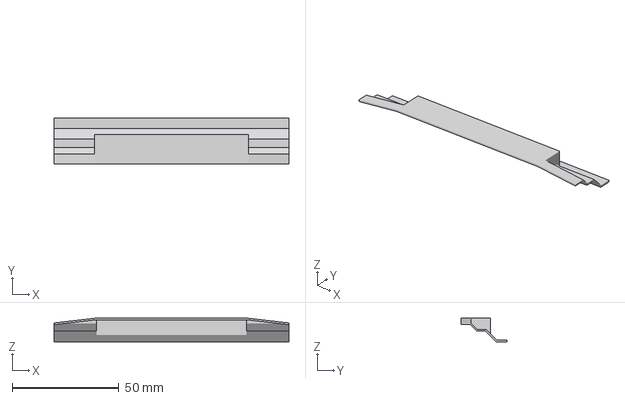
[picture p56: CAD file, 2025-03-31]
fab/3d/3mf/Weichenabdeckung_2Weg_1_v4.3mf
110.0 x 21.8 x 11.0 mm

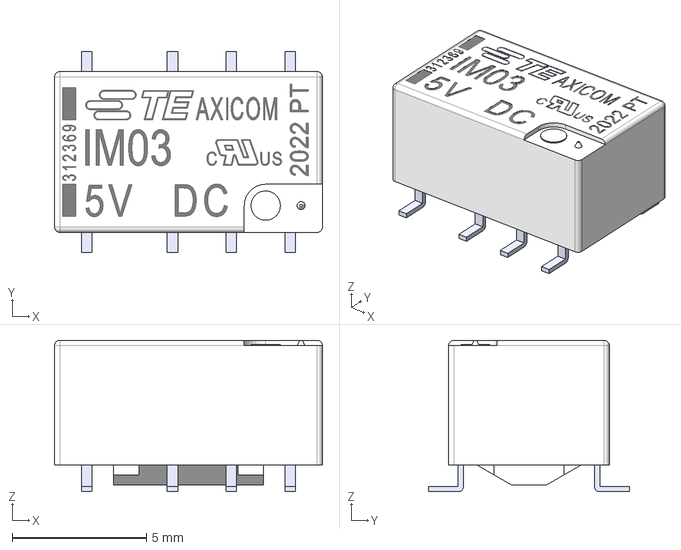
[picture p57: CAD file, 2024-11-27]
fab/kicad/3D/Relays/IM03GR Relay (TE Connectivity).step
10.0 x 7.50 x 5.65 mm

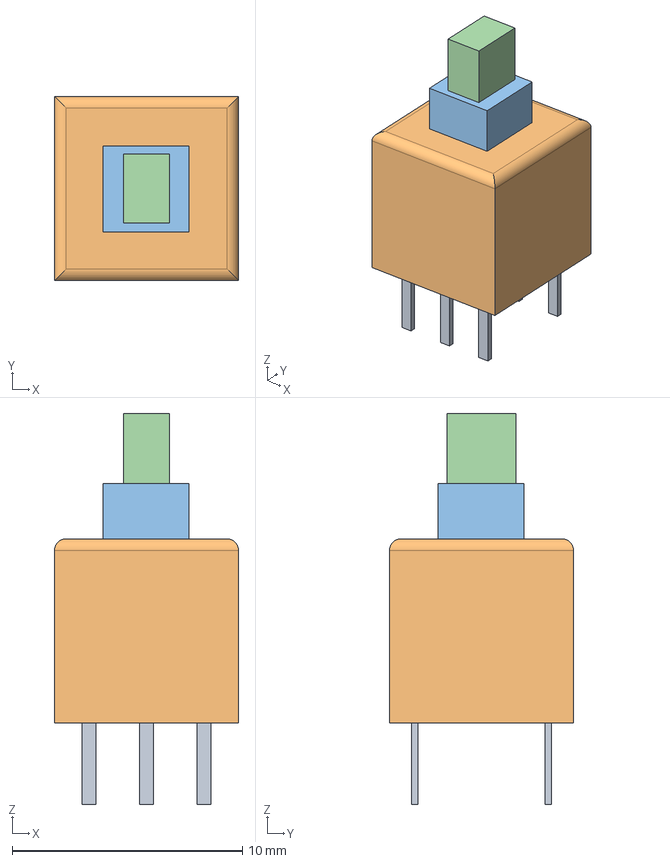
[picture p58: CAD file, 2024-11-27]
fab/kicad/3D/SW_Push_DPDT_8x8_v3.step
8.00 x 8.00 x 17.0 mm

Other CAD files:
fab/3d/Rahmen_Back_N__2xP20_230mm_261008.FCStd
fab/3d/3mf/Weichenabdeckung_2Weg_flach v1.3mf
fab/3d/Rahmen_SeiteZweigleisig_260906.FCStd
fab/3d/3mf/Biegelehre_LED v4.3mf
fab/3d/3mf/Bracket_sub-D_250209.3mf
fab/3d/3mf/ModulSeite_250209.3mf
fab/3d/3mf/OLED_Mount_260313.3mf
fab/3d/3mf/Querverstrebung_250209.3mf
fab/3d/Biegelehre_LED.FCStd
fab/3d/Bohrhilfe_klein_251114.FCStd
fab/3d/Bracket_sub-D.FCStd
fab/3d/Klammer265.FCStd
fab/3d/ModulSeiteEingleisig.FCStd
fab/3d/ModulSeiteEingleisig_251109.FCStd
fab/3d/ModulSeiteZweigleisig_251109.FCStd
fab/3d/ModulStützeEingleisig_251109.FCStd
fab/3d/ModulStützeEingleisig_260427.FCStd
fab/3d/ModulStützeZweigleisig_251109.FCStd
fab/3d/ModulStützeZweigleisig_260427.FCStd
fab/3d/OLED_Mount_260313.FCStd
fab/3d/Querverstrebung_23cm.FCStd
fab/3d/Rahmen_SeiteEingleisig_260906.FCStd
fab/3d/f3d/Biegelehre_LED v4.f3d
fab/3d/f3d/Querverstrebung_230mm_250606.f3d
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

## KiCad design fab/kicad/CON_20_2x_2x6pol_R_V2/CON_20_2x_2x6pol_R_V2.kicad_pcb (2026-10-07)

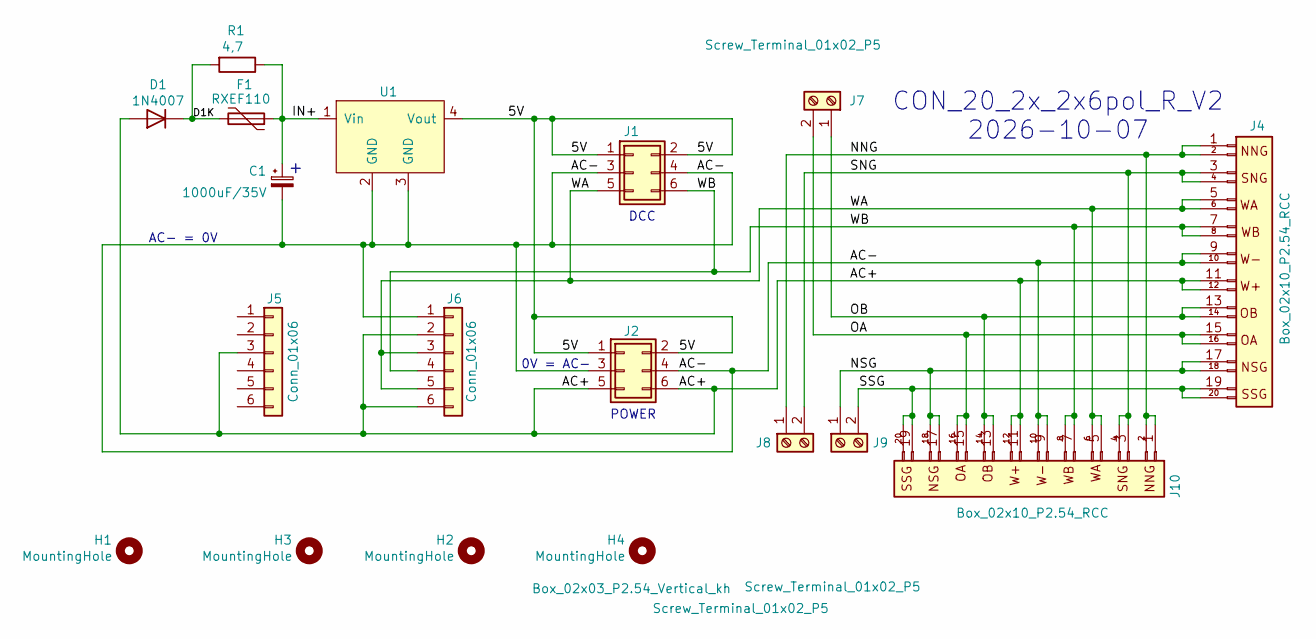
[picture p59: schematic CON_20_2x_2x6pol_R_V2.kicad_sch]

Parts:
C1: 1000uF/35V; CP_Radial_L16.8mm_D10.0mm_P5.08mm_Horizontal_small_2
D1: 1N4007; D_DO-41_SOD81_P12.7mm_Horizontal_kh
F1: RXEF110; Fuse_PTC_P5.08mm_D12.8mm_Horizontal_kh
H1, H2, H3, H4: MountingHole; MountingHole_2.7mm_M2.5_DIN965_Pad_TopBottom
J1: Box_02x03_P2.54_Vertical; Box_02x03_P2.54mm_Vertical_kh
J2: Box_02x03_P2.54_Vertical_kh; Box_02x03_P2.54mm_Vertical_kh
J4, J10: Box_02x10_P2.54_RCC; Box_02x10_P2.54mm_Vertical_kh
J5, J6: Conn_01x06; PinSocket_1x06_P2.54mm_Vertical_kh
J7, J8: Screw_Terminal_01x02_P5
J9: Screw_Terminal_01x02_P5; Screw_Terminal_01x02_P5_8
R1: 4,7; R_Axial_Power_L25.0mm_W6.4mm_P27.94mm_kh
U1: DCDC_StepDown_LM2596; DCDC_StepDown_LM2596_PinsOnly

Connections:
/5V: J1.1, J1.2, J2.1, J2.2, U1.4 (Vout)
/AC+: D1.2 (A), J2.5, J2.6, J4.11, J4.12, J5.3 (Pin_3_3), J6.2, J6.6, J10.11, J10.12
/AC-: C1.2, J1.3, J1.4, J2.3, J2.4, J4.9, J4.10, J6.1, J10.9, J10.10, U1.2 (GND), U1.3 (GND)
/D1K: D1.1 (K), F1.2, R1.2
/IN+: C1.1, F1.1, R1.1, U1.1 (Vin)
/NNG: J4.1, J4.2, J8.1, J10.1, J10.2
/NSG: J4.17, J4.18, J9.1, J10.17, J10.18
/OA: J4.15, J4.16, J7.2, J10.15, J10.16
/OB: J4.13, J4.14, J7.1, J10.13, J10.14
/SNG: J4.3, J4.4, J8.2, J10.3, J10.4
/SSG: J4.19, J4.20, J9.2, J10.19, J10.20
/WA: J1.5, J4.5, J4.6, J6.3, J6.5, J10.5, J10.6
/WB: J1.6, J4.7, J4.8, J6.4, J10.7, J10.8

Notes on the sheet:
AC- = 0V
POWER
CON_20_2x_2x6pol_R_V2 2026-10-07
0V = AC-
DCC

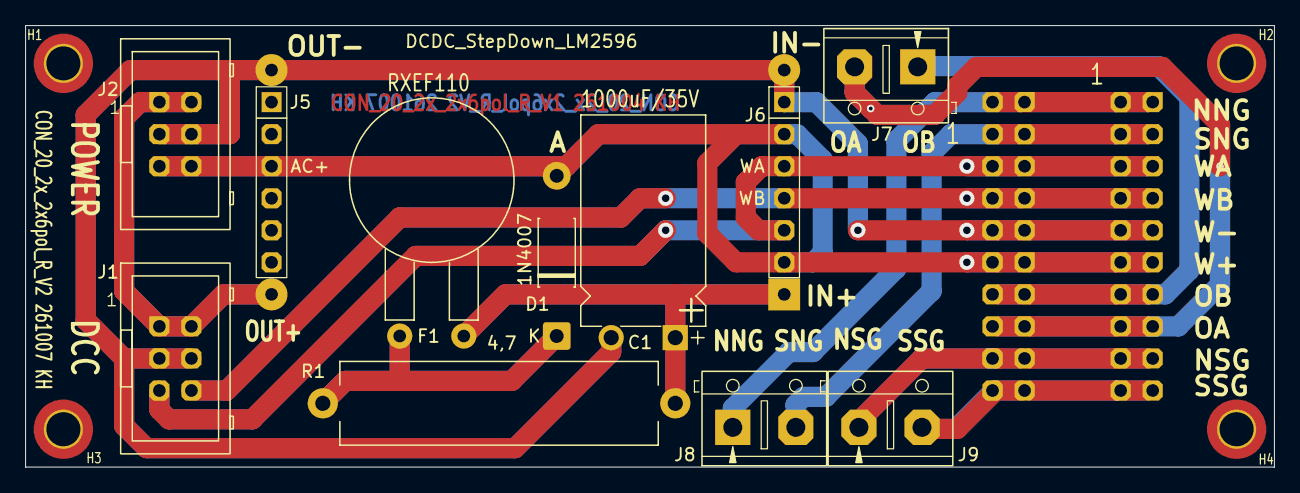
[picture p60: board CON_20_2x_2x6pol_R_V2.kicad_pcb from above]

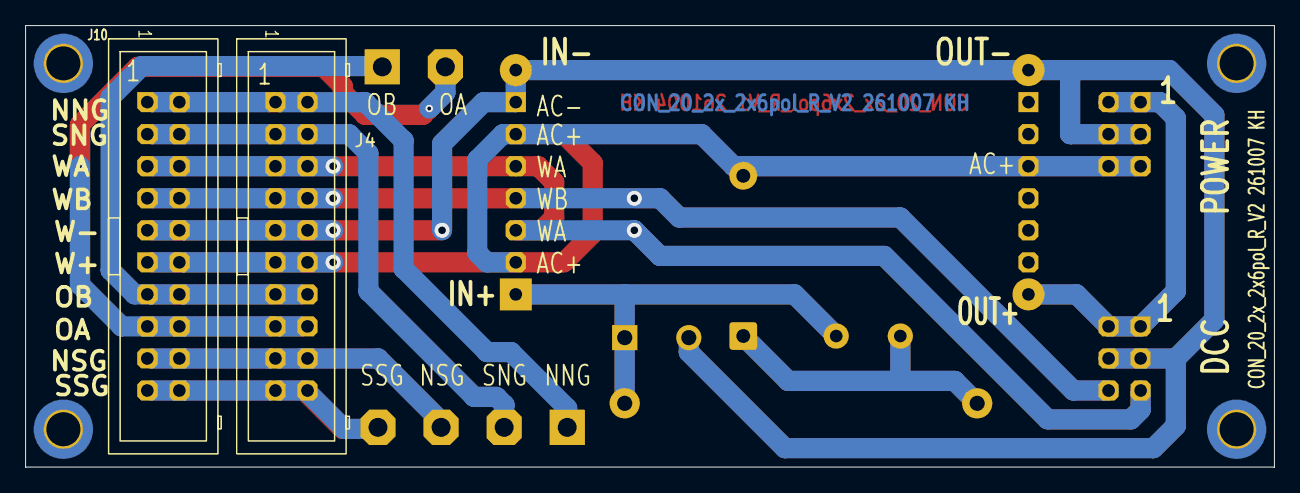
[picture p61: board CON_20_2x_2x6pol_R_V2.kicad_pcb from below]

Board: 2 copper layers, 99.0 x 35.0 mm, 18 parts (2 on the bottom side), 13 nets.

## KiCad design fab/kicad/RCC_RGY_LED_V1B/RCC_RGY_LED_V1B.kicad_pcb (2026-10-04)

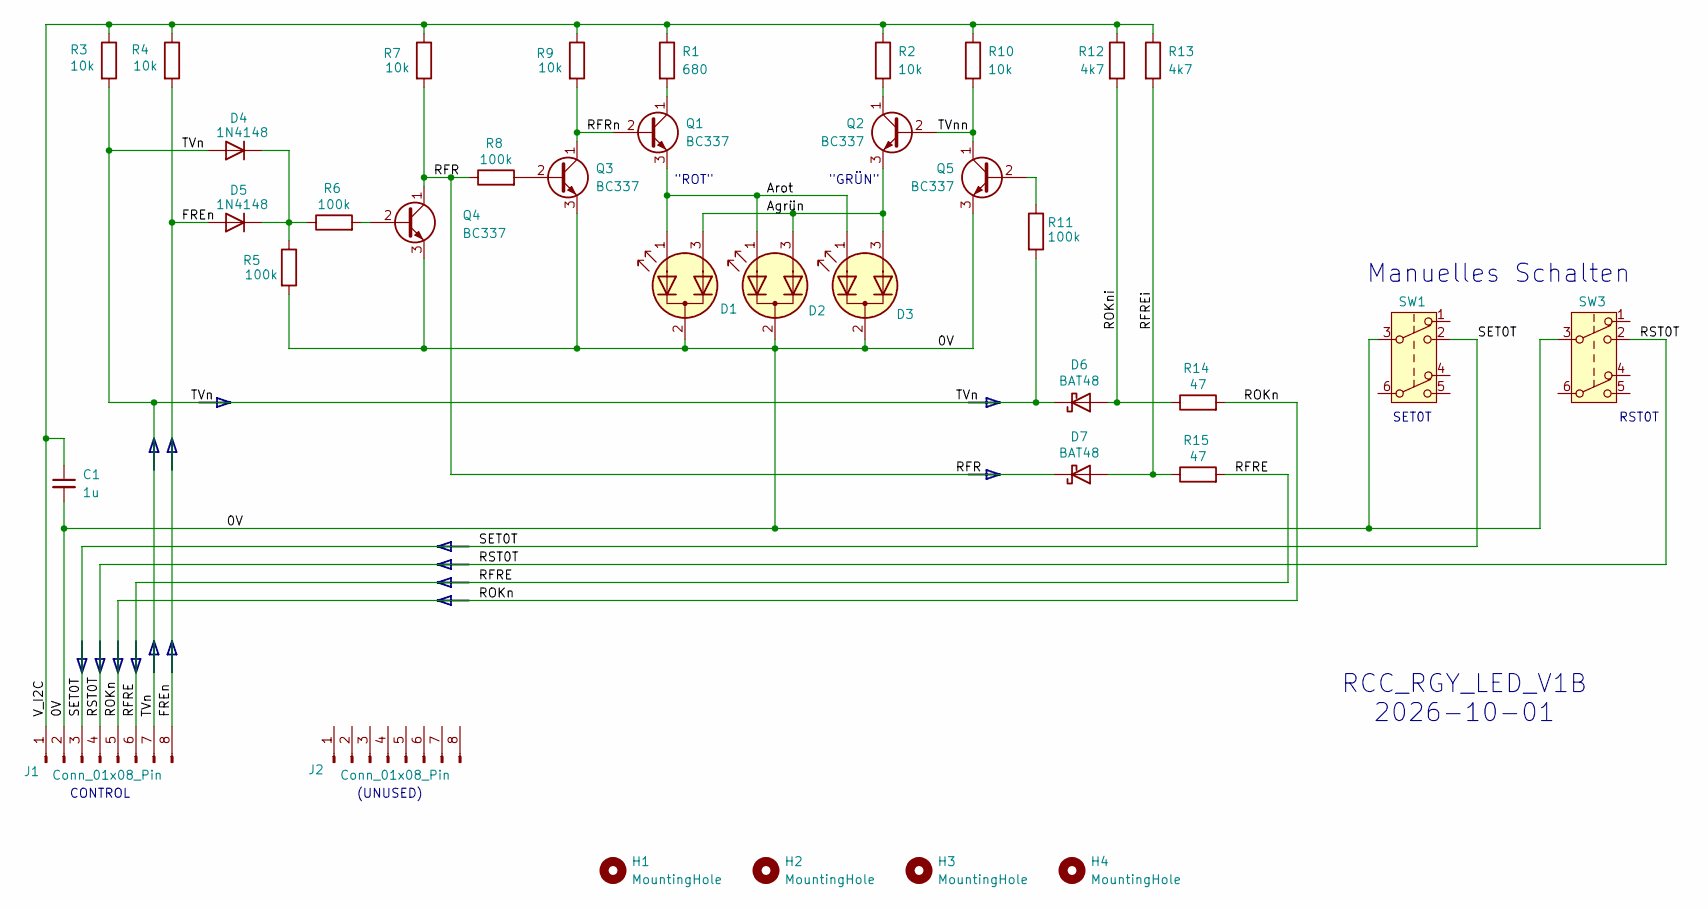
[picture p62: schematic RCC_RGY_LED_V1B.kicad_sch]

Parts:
C1: 1u; C_L4.3mm_D2.8mm_P5.08mm_kh
D1, D2, D3: LED_Dual_AKA; LED_D5.0mm-3
D4: 1N4148; D_DO-35_P3.81mm_Vertical_AnodeUp_kh
D5: 1N4148; D_DO-35_P2.0mm_Vertical_AnodeUp_kh
D6, D7: BAT48; D_DO-35_SOD27_P2.54mm_Vertical_AnodeUp_kh
H1, H2, H3, H4: MountingHole; MountingHole_2.2mm_M2_Pad_TopBottom_kh
J1, J2: Conn_01x08_Pin; PinSocket_1x08_P2.54mm_Vertical_11mm_kh
Q1, Q2, Q3, Q4, Q5: BC337; TO-92_Inline_Wide_custom
R1: 680; R_Axial_DIN0204_L3.6mm_D1.6mm_P2.54mm_Vertical_kh
R2, R3, R9, R10: 10k; R_Axial_DIN0204_L3.6mm_D1.6mm_P2.54mm_Vertical
R4: 10k; R_Axial_DIN0204_L3.6mm_D1.6mm_P17.78mm_Horizontal
R5, R11: 100k; R_Axial_DIN0204_L3.6mm_D1.6mm_P2.54mm_Vertical
R6: 100k; R_Axial_DIN0204_L3.6mm_D1.6mm_P2.54mm_Vertical_kh
R7: 10k; R_Axial_DIN0204_L3.6mm_D1.6mm_P7.62mm_Horizontal
R8: 100k; R_Axial_DIN0204_L3.6mm_D1.6mm_P3.81mm_Vertical_kh
R12: 4k7; R_Axial_DIN0204_L3.6mm_D1.6mm_P2.54mm_Vertical
R13: 4k7; R_Axial_DIN0204_L3.6mm_D1.6mm_P3.81mm_Vertical_kh
R14: 47; R_Axial_DIN0204_L3.6mm_D1.6mm_P2.54mm_Vertical_kh
R15: 47; R_Axial_DIN0204_L3.6mm_D1.6mm_P7.62mm_Horizontal
SW1, SW3: SW_Push_DPDT_8x8

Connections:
/0V: C1.2, D1.2 (K), D2.2 (K), D3.2 (K), J1.2, Q3.3 (E), Q4.3 (E), Q5.3 (E), R5.2, SW1.3 (C), SW3.3 (C)
/Agrün: D1.3 (A2), D2.3 (A2), D3.3 (A2), Q2.3 (E)
/Arot: D1.1 (A1), D2.1 (A1), D3.1 (A1), Q1.3 (E)
/FREn: D5.2 (A), J1.8, R4.2
/RFR: D7.1 (K), Q4.1 (C), R7.2, R8.1
/RFRE: J1.6, R15.2
/RFREi: D7.2 (A), R13.2, R15.1
/RFRn: Q1.2 (B), Q3.1 (C), R9.2
/ROKn: J1.5, R14.2
/ROKni: D6.2 (A), R12.2, R14.1
/RST0T: J1.4, SW3.2 (B)
/SET0T: J1.3, SW1.2 (B)
/TVn: D4.2 (A), D6.1 (K), J1.7, R3.2, R11.2
/TVnn: Q2.2 (B), Q5.1 (C), R10.2
/V_I2C: C1.1, J1.1, R1.1, R2.1, R3.1, R4.1, R7.1, R9.1, R10.1, R12.1, R13.1
unnamed: D4.1 (K), D5.1 (K), R5.1, R6.1
unnamed: Q1.1 (C), R1.2
unnamed: Q2.1 (C), R2.2
unnamed: Q3.2 (B), R8.2
unnamed: Q4.2 (B), R6.2
unnamed: Q5.2 (B), R11.1

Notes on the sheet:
(UNUSED)
SET0T
Manuelles Schalten
"GRÜN"
RCC_RGY_LED_V1B 2026-10-01
CONTROL
"ROT"
RST0T

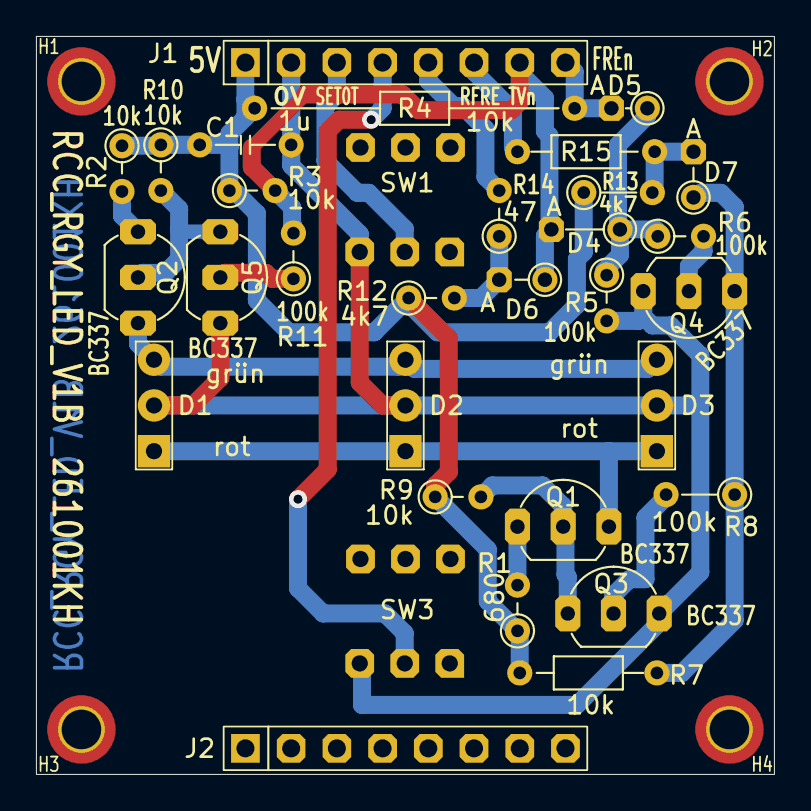
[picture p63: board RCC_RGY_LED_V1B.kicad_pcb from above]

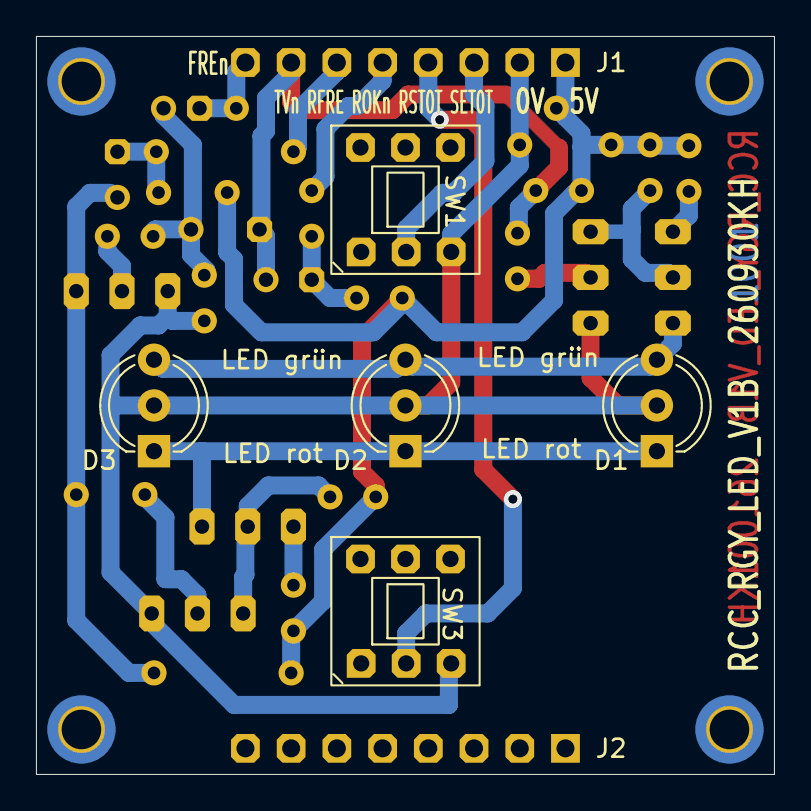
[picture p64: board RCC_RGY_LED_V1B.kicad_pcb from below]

Board: 2 copper layers, 41.0 x 41.0 mm, 36 parts (5 on the bottom side), 21 nets.

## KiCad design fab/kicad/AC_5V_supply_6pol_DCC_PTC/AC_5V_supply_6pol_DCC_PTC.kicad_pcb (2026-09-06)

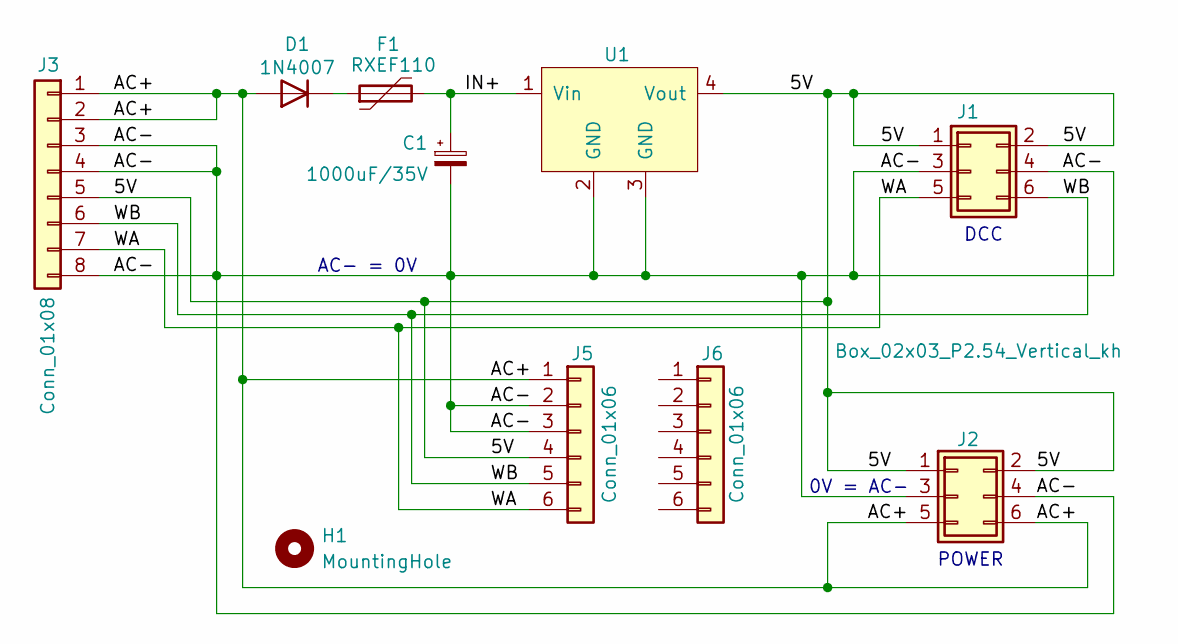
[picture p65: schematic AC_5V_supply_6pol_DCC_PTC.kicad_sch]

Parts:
C1: 1000uF/35V; CP_Radial_L16.8mm_D10.0mm_P5.08mm_Horizontal_small_2
D1: 1N4007; D_DO-41_P5.08mm_Vertical_AnodeUp_kh
F1: RXEF110; Fuse_PTC_P5.08mm_D12.8mm_Horizontal_kh
H1: MountingHole; MountingHole_2.7mm_M2.5_DIN965_Pad_TopBottom
J1: Box_02x03_P2.54_Vertical; Box_02x03_P2.54mm_Vertical_kh
J2: Box_02x03_P2.54_Vertical_kh; Box_02x03_P2.54mm_Vertical_kh
J3: Conn_01x08; PinSocket_1x08_P2.54mm_Vertical_kh
J5, J6: Conn_01x06; PinSocket_1x06_P2.54mm_Vertical_kh
U1: DCDC_StepDown_LM2596; DCDC_StepDown_LM2596_PinsOnly

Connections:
/5V: J1.1, J1.2, J2.1, J2.2, J3.5, J5.4, U1.4 (Vout)
/AC+: D1.2 (A), J2.5, J2.6, J3.1, J3.2, J5.1
/AC-: C1.2, J1.3, J1.4, J2.3, J2.4, J3.3, J3.4, J3.8, J5.2, J5.3, U1.2 (GND), U1.3 (GND)
/IN+: C1.1, F1.2, U1.1 (Vin)
/WA: J1.5, J3.7, J5.6
/WB: J1.6, J3.6, J5.5
unnamed: D1.1 (K), F1.1

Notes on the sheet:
AC- = 0V
POWER
0V = AC-
DCC

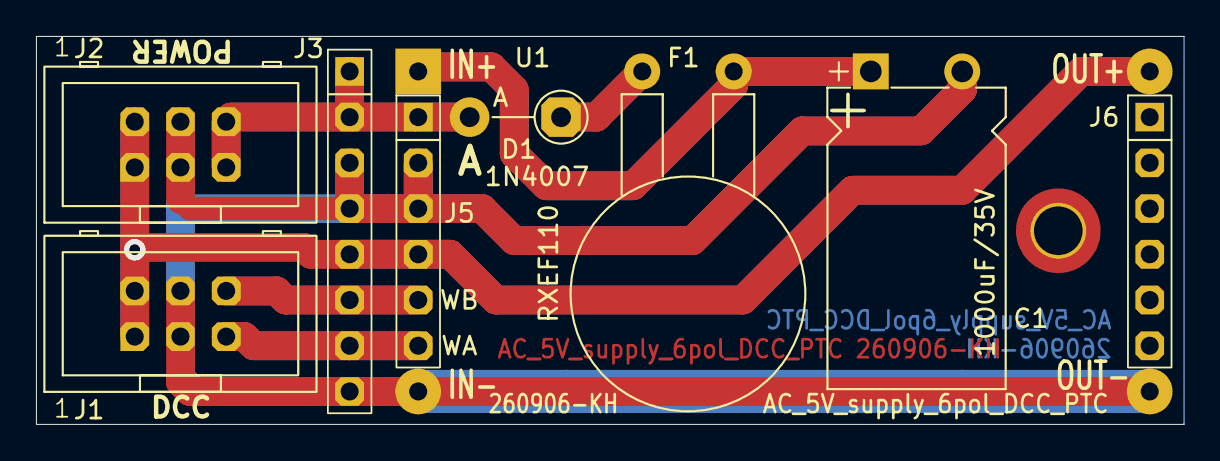
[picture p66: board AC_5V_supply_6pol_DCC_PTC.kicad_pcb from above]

Board: 2 copper layers, 63.8 x 21.6 mm, 10 parts (0 on the bottom side), 7 nets.

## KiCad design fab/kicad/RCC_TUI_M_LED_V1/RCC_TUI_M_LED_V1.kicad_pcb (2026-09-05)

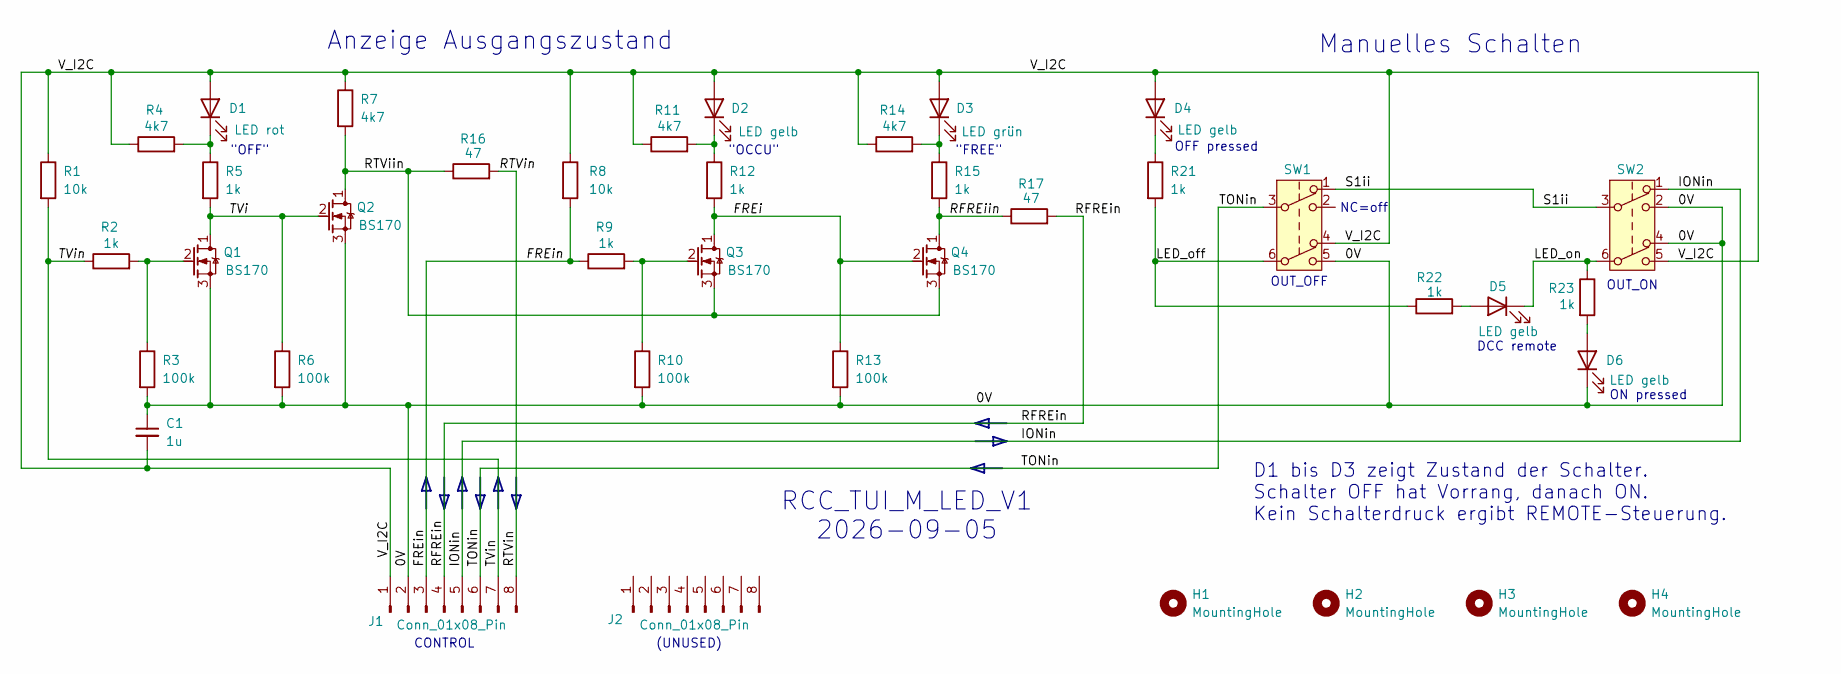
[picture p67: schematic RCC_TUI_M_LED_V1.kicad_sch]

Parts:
C1: 1u; C_L4mm_D3mm_P2.54mm_kh
D1: LED rot; LED_D3.0mm_kh
D2, D4, D5, D6: LED gelb; LED_D3.0mm_kh
D3: LED grün; LED_D3.0mm_kh
H1, H2, H3, H4: MountingHole; MountingHole_2.2mm_M2_Pad_TopBottom_kh
J1, J2: Conn_01x08_Pin; PinSocket_1x08_P2.54mm_Vertical_11mm_kh
Q1, Q2, Q3, Q4: BS170; TO-92_Inline_Wide_custom
R1: 10k; R_Axial_DIN0204_L3.6mm_D1.6mm_P2.54mm_Vertical
R2, R5, R9, R21, R22, R23: 1k; R_Axial_DIN0204_L3.6mm_D1.6mm_P2.54mm_Vertical_kh
R3, R6, R10, R13: 100k; R_Axial_DIN0204_L3.6mm_D1.6mm_P2.54mm_Vertical
R4, R11, R14: 4k7; R_Axial_DIN0204_L3.6mm_D1.6mm_P2.54mm_Vertical_kh
R7: 4k7; R_Axial_DIN0204_L3.6mm_D1.6mm_P2.54mm_Vertical
R8: 10k; R_Axial_DIN0204_L3.6mm_D1.6mm_P2.54mm_Vertical_kh
R12, R15: 1k; R_Axial_DIN0204_L3.6mm_D1.6mm_P2.54mm_Vertical
R16: 47; R_Axial_DIN0204_L3.6mm_D1.6mm_P3.81mm_Vertical_kh
R17: 47; R_Axial_DIN0207_L6.3mm_D2.5mm_P12.7mm_Horizontal_kh
SW1, SW2: SW_Push_DPDT_8x8

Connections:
/0V: C1.1, D6.1 (K), J1.2, Q1.3 (S), Q2.3 (S), R3.2, R6.2, R10.2, R13.2, SW1.5 (B), SW2.2 (B), SW2.4 (A)
/FREi: Q3.1 (D), Q4.2 (G), R12.2, R13.1
/FREin: J1.3, R8.2, R9.1
/IONin: J1.5, SW2.1 (A)
/LED_off: R21.2, R22.1, SW1.6 (C)
/LED_on: D5.1 (K), R23.1, SW2.6 (C)
/RFREiin: Q4.1 (D), R15.2, R17.1
/RFREin: J1.4, R17.2
/RTViin: Q2.1 (D), Q3.3 (S), Q4.3 (S), R7.2, R16.1
/RTVin: J1.8, R16.2
/S1ii: SW1.1 (A), SW2.3 (C)
/TONin: J1.6, SW1.3 (C)
/TVi: Q1.1 (D), Q2.2 (G), R5.2, R6.1
/TVin: J1.7, R1.2, R2.1
/V_I2C: C1.2, D1.2 (A), D2.2 (A), D3.2 (A), D4.2 (A), J1.1, R1.1, R4.1, R7.1, R8.1, R11.1, R14.1, SW1.4 (A), SW2.5 (B)
unnamed: D1.1 (K), R4.2, R5.1
unnamed: D2.1 (K), R11.2, R12.1
unnamed: D3.1 (K), R14.2, R15.1
unnamed: D4.1 (K), R21.1
unnamed: D5.2 (A), R22.2
unnamed: D6.2 (A), R23.2
unnamed: Q1.2 (G), R2.2, R3.1
unnamed: Q3.2 (G), R9.2, R10.1

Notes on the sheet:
ON pressed
(UNUSED)
OUT_OFF
"OCCU"
D1 bis D3 zeigt Zustand der Schalter. Schalter OFF hat Vorrang, danach ON. Kein Schalterdruck ergibt REMOTE-Steuerung.
Manuelles Schalten
"OFF"
CONTROL
OUT_ON
OFF pressed
Anzeige Ausgangszustand
"FREE"
RCC_TUI_M_LED_V1 2026-09-05
DCC remote
NC=off

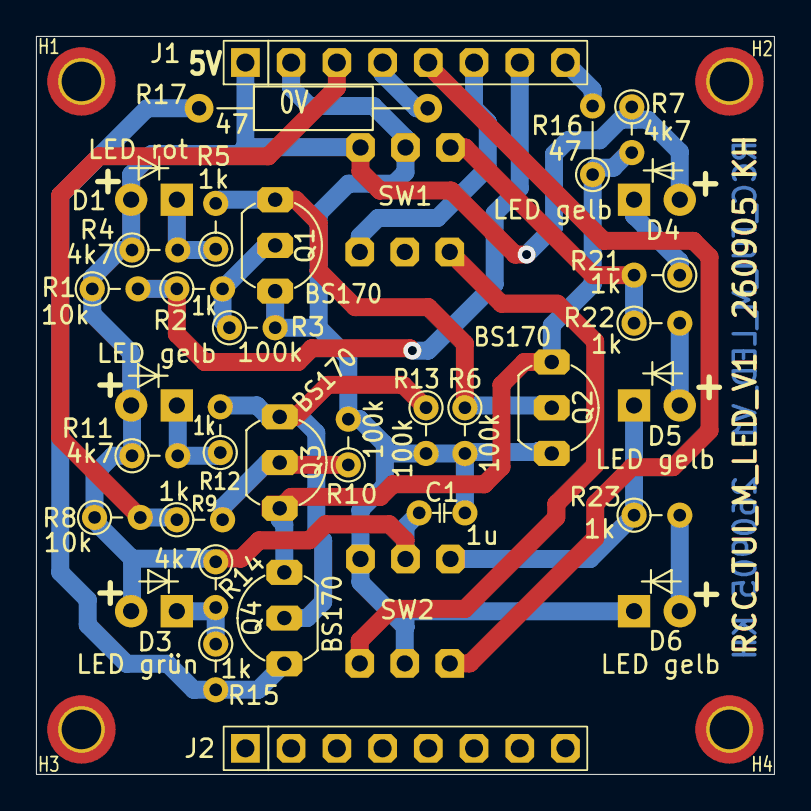
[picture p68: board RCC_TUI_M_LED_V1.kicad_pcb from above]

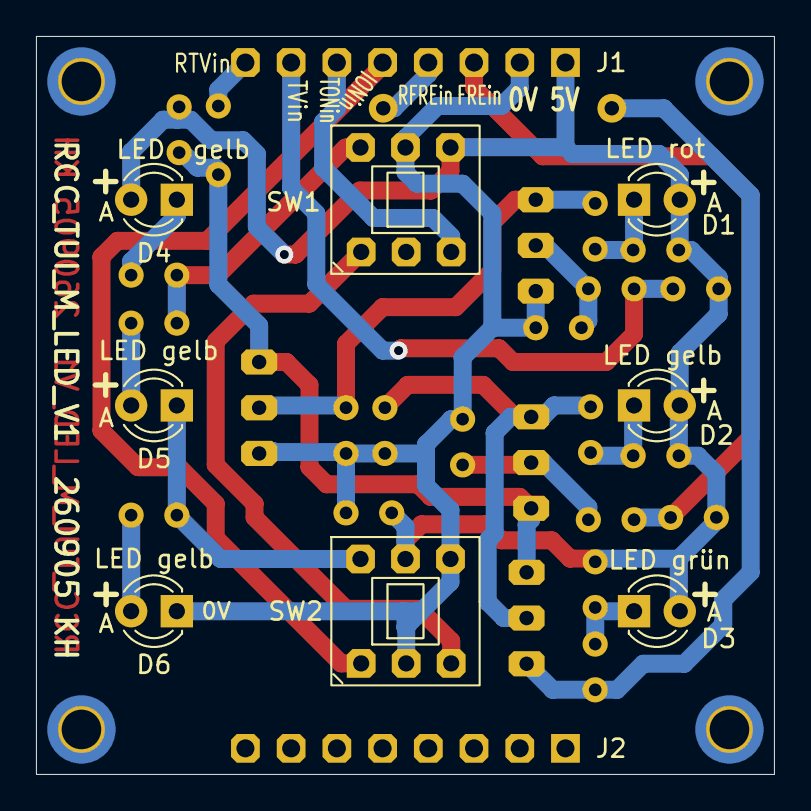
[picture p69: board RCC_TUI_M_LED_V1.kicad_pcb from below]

Board: 2 copper layers, 41.0 x 41.0 mm, 39 parts (8 on the bottom side), 23 nets.

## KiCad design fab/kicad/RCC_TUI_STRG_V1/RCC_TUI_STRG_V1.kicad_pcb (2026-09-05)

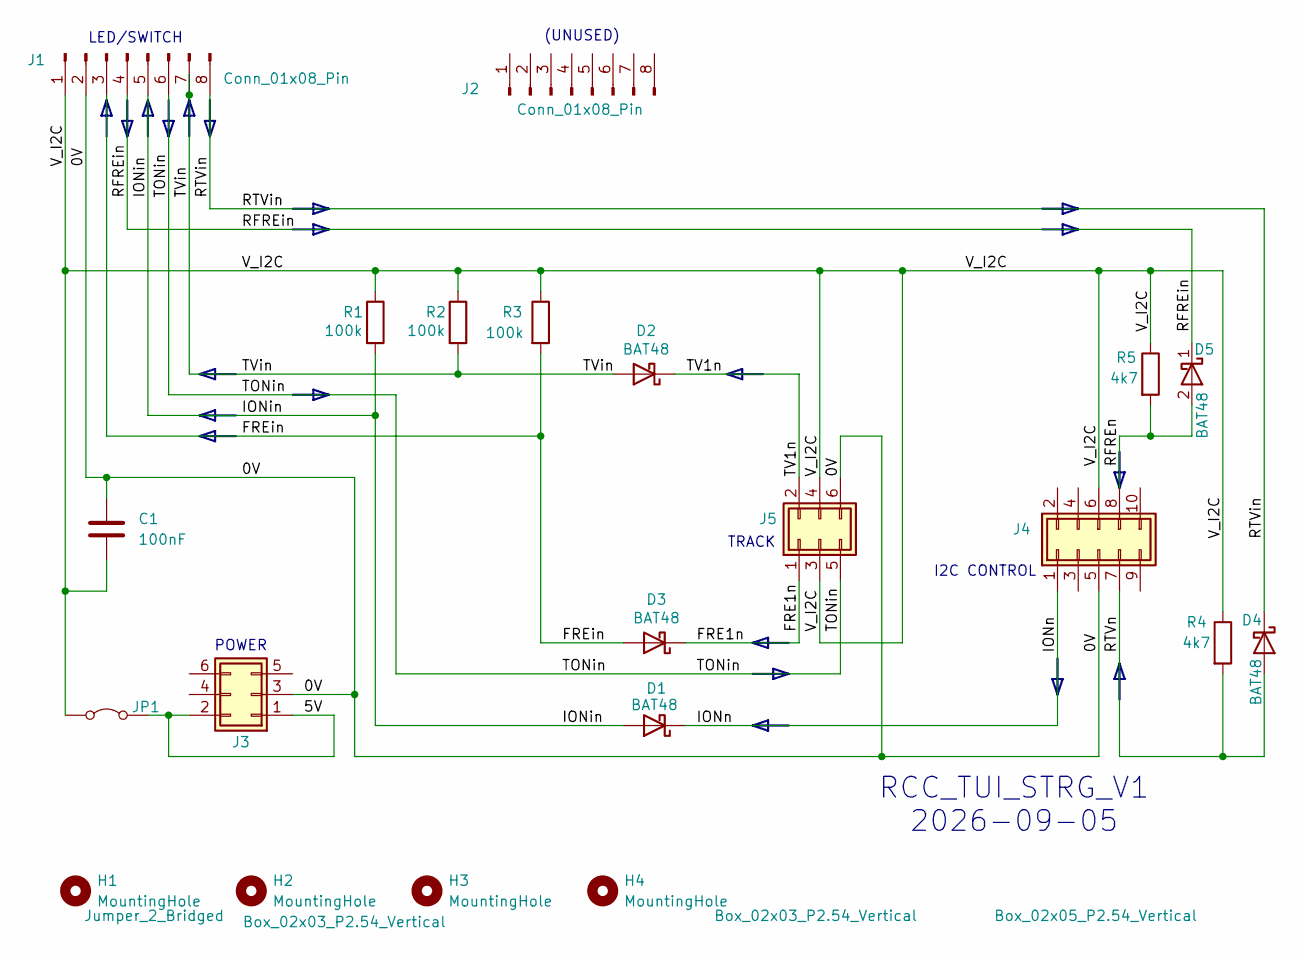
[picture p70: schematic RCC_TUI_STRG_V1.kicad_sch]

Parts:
C1: 100nF; C_Rect_L7.0mm_W2.0mm_P5.00mm_kh
D1, D2, D3, D4: BAT48; D_DO-35_P7.62mm_Horizontal_kh
D5: BAT48; D_DO-35_P12.7mm_Horizontal_kh
H1, H2, H3, H4: MountingHole; MountingHole_2.2mm_M2_Pad_TopBottom_kh
J1, J2: Conn_01x08_Pin; PinSocket_1x08_P2.54mm_Vertical_kh
J3, J5: Box_02x03_P2.54_Vertical; Box_02x03_P2.54mm_Vertical_kh
J4: Box_02x05_P2.54_Vertical; Box_02x05_P2.54mm_Vertical_kh
JP1: Jumper_2_Bridged; SolderJumper-2_P1.3mm_Bridged_Pad1.0x1.5mm
R1: 100k; R_Axial_P5.08_Vertical_kh
R2, R3: 100k; R_Axial_DIN0204_L3.6mm_D1.6mm_P2.54mm_Vertical_kh
R4, R5: 4k7; R_Axial_DIN0204_L3.6mm_D1.6mm_P2.54mm_Vertical_kh

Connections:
/0V: C1.1, J1.2, J3.3, J4.5, J5.6
/5V: J3.1, J3.2, JP1.2 (B)
/FRE1n: D3.1 (K), J5.1
/FREin: D3.2 (A), J1.3, R3.2
/IONin: D1.2 (A), J1.5, R1.2
/IONn: D1.1 (K), J4.1
/RFREin: D5.1 (K), J1.4
/RFREn: D5.2 (A), J4.8, R5.2
/RTVin: D4.1 (K), J1.8
/RTVn: D4.2 (A), J4.7, R4.2
/TONin: J1.6, J5.5
/TV1n: D2.1 (K), J5.2
/TVin: D2.2 (A), J1.7, R2.2
/V_I2C: C1.2, J1.1, J4.6, J5.3, J5.4, JP1.1 (A), R1.1, R2.1, R3.1, R4.1, R5.1

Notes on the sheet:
TRACK
RCC_TUI_STRG_V1 2026-09-05
I2C CONTROL
POWER
(UNUSED)
LED/SWITCH


Board: 2 copper layers, 41.0 x 41.0 mm, 21 parts (1 on the bottom side), 14 nets.

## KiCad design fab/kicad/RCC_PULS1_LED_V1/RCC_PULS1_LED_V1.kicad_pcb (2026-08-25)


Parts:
C1: 100n; C_L4mm_D3mm_P2.54mm_kh
D1, D4: LED gelb; LED_D3.0mm
D2, D5: LED grün; LED_D3.0mm
H1, H2, H3, H4: MountingHole; MountingHole_2.2mm_M2_Pad_TopBottom_kh
J1, J2: Conn_01x08_Pin; PinSocket_1x08_P2.54mm_Vertical_11mm_kh
Q1, Q2: BC337; TO-92_Inline_Wide_custom
R1, R6, R8: 1k; R_Axial_DIN0204_L3.6mm_D1.6mm_P10,16mm_Horizontal
R2: 100k; R_Axial_DIN0204_L3.6mm_D1.6mm_P3.81mm_Vertical_kh
R3: 1k; R_Axial_DIN0204_L3.6mm_D1.6mm_P2.54mm_Vertical_kh
R4, R9: 10k; R_Axial_DIN0204_L3.6mm_D1.6mm_P2.54mm_Vertical_kh
R5: 47; R_Axial_DIN0204_L3.6mm_D1.6mm_P2.54mm_Vertical_kh
R7: 100k; R_Axial_DIN0204_L3.6mm_D1.6mm_P7.62mm_Horizontal
R10: 47; R_Axial_DIN0204_L3.6mm_D1.6mm_P2.54mm_Vertical

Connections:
/0V: C1.2, J1.2, Q1.3 (E), Q2.3 (E)
/PS1: J1.8, R1.2, R2.1
/PS2: J1.7, R6.2, R7.1
/Q1C: Q1.1 (C), R3.2, R5.1
/Q2C: Q2.1 (C), R8.2, R10.1
/RPS1: J1.6, R5.2
/RPS2: J1.5, R10.2
/V_I2C: C1.1, D1.2 (A), D2.2 (A), D4.2 (A), D5.2 (A), J1.1, R4.1, R9.1
unnamed: D1.1 (K), R8.1, R9.2
unnamed: D2.1 (K), R6.1
unnamed: D4.1 (K), R3.1, R4.2
unnamed: D5.1 (K), R1.1
unnamed: Q1.2 (B), R2.2
unnamed: Q2.2 (B), R7.2

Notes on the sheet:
LED/SWITCH
(UNUSED)
RCC_PULS1_LED_V1 2026-08-25
"PULS2 da!"
"PULS1 da!"
"Kein Puls2"
"Kein Puls1"



Board: 2 copper layers, 41.0 x 41.0 mm, 23 parts (4 on the bottom side), 14 nets.

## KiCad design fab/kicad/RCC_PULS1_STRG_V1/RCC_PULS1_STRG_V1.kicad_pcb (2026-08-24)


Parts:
C1, C2: 100nF; C_Rect_L7.0mm_W2.0mm_P5.00mm_kh
C3, C4: 10u; ELKO_L4.32mm_D3.81mm_P2.54mm_kh
D1, D2, D3: BAT48; D_DO-35_P2.0mm_Vertical_AnodeUp_kh
D4, D5, D6, D7, D8, D9, D10: BAT48; D_DO-35_SOD27_P2.54mm_Vertical_AnodeUp_kh
H1, H2, H3, H4: MountingHole; MountingHole_2.2mm_M2_Pad_TopBottom_kh
J1, J2: Conn_01x08_Pin; PinSocket_1x08_P2.54mm_Vertical_kh
J3, J5: Box_02x03_P2.54_Vertical; Box_02x03_P2.54mm_Vertical_kh
J4: Box_02x05_P2.54_Vertical; Box_02x05_P2.54mm_Vertical_kh
JP1: Jumper_2_Bridged; SolderJumper-2_P1.3mm_Bridged_Pad1.0x1.5mm
Q1, Q2: BC337; TO-92_Inline_Wide_custom
R1, R5: 10k; R_Axial_DIN0204_L3.6mm_D1.6mm_P2.54mm_Vertical
R2, R6: 10k; R_Axial_DIN0204_L3.6mm_D1.6mm_P2.54mm_Vertical_kh
R3: 4k7; R_Axial_DIN0204_L3.6mm_D1.6mm_P2.54mm_Vertical
R4: 4k7; R_Axial_DIN0204_L3.6mm_D1.6mm_P3.81mm_Vertical_kh
R7, R8: 1k; R_Axial_DIN0204_L3.6mm_D1.6mm_P2.54mm_Vertical_kh
RV1, RV2: 500k; Trim_RM-063_Horizontal_kh
U1: 4538_kh; DIP-16_W7.62mm_kh

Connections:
/0V: C1.1, C2.1, C3.2, C4.2, J1.2, J3.3, J4.5, J5.5, J5.6, Q1.3 (E), Q2.3 (E), U1.1 (CX), U1.4 (B), U1.8 (VSS), U1.12 (B), U1.15 (CX)
/5V: J3.1, J3.2, JP1.2 (B)
/IN1n: D1.2 (A), D2.2 (A), D6.1 (K), R1.2, U1.5 (A)
/IN2n: D3.2 (A), D4.2 (A), D9.1 (K), R2.2, U1.11 (A)
/PS1: J1.8, Q1.1 (C), R7.2
/PS1g: D5.2 (A), D6.2 (A), D7.2 (A), R5.2
/PS1i: D2.1 (K), J4.1
/PS2: J1.7, Q2.1 (C), R8.2
/PS2g: D8.2 (A), D9.2 (A), D10.2 (A), R6.2
/PS2i: D4.1 (K), J4.2
/RC1n: C3.1, R3.2, U1.2 (Rx)
/RC2n: C4.1, R4.2, U1.14 (Rx)
/RD1n: D1.1 (K), J5.1
/RD2n: D3.1 (K), J5.2
/RPS1: J1.6, J4.7
/RPS2: J1.5, J4.8
/V_I2C: C1.2, C2.2, J1.1, J4.6, J5.3, J5.4, JP1.1 (A), R1.1, R2.1, R5.1, R6.1, R7.1, R8.1, RV1.1, RV1.2, RV2.1, RV2.2, U1.3 (R), U1.13 (R), U1.16 (VDD)
unnamed: D5.1 (K), U1.7 (Q)
unnamed: D7.1 (K), Q1.2 (B)
unnamed: D8.1 (K), U1.9 (Q)
unnamed: D10.1 (K), Q2.2 (B)
unnamed: R3.1, RV1.3
unnamed: R4.1, RV2.3

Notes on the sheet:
ZUM REED
RCC_PULS1_STRG_V1 2026-08-24
I2C CONTROL
POWER
(UNUSED)
LED/SWITCH


Board: 2 copper layers, 41.0 x 41.0 mm, 37 parts (0 on the bottom side), 23 nets.

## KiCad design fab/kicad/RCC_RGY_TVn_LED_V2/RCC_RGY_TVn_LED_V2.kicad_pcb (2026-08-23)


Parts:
C1: 1u; C_L4mm_D3mm_P2.54mm_kh
D1, D2, D3: LED_Dual_AKA; LED_D5.0mm-3
D4: BAT48; D_DO-35_SOD27_P2.54mm_Vertical_AnodeUp
H1, H2, H3, H4: MountingHole; MountingHole_2.2mm_M2_Pad_TopBottom_kh
J1, J2: Conn_01x08_Pin; PinSocket_1x08_P2.54mm_Vertical_11mm_kh
Q1, Q6: BC337; TO-92_Inline_Wide_custom
Q2, Q3, Q4, Q5: BC327; TO-92_Inline_Wide_custom
R1: 1k; R_Axial_DIN0204_L3.6mm_D1.6mm_P7.62mm_Horizontal
R2, R3, R5: 10k; R_Axial_DIN0204_L3.6mm_D1.6mm_P2.54mm_Vertical
R4, R14, R15: 100k; R_Axial_DIN0204_L3.6mm_D1.6mm_P2.54mm_Vertical
R6, R8: 4k7; R_Axial_DIN0204_L3.6mm_D1.6mm_P2.54mm_Vertical_kh
R7: 4k7; R_Axial_DIN0204_L3.6mm_D1.6mm_P3.81mm_Vertical_kh
R9: 47; R_Axial_DIN0204_L3.6mm_D1.6mm_P2.54mm_Vertical_kh
R10, R12: 4k7; R_Axial_DIN0204_L3.6mm_D1.6mm_P2.54mm_Vertical
R11: 100k; R_Axial_DIN0204_L3.6mm_D1.6mm_P7.62mm_Horizontal
R13: 47; R_Axial_DIN0204_L3.6mm_D1.6mm_P7.62mm_Horizontal
SW1, SW3: SW_Push_DPDT_8x8

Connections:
/0V: C1.2, D1.2 (K), D2.2 (K), D3.2 (K), J1.2, Q4.1 (C), Q5.1 (C), Q6.3 (E), SW1.3 (C), SW3.3 (C)
/Agrün: D1.3 (A2), D2.3 (A2), D3.3 (A2), R3.2
/Arot: D1.1 (A1), D2.1 (A1), D3.1 (A1), Q1.3 (E)
/FREn: J1.8, R7.1, R15.2
/RFRE: J1.6, R13.2
/ROKn: D4.2 (A), J1.5, R10.2
/RST0T: J1.4, SW3.2 (B)
/SET0T: J1.3, SW1.2 (B)
/TVn: J1.7, R6.2, R8.1, R14.2
/V_I2C: C1.1, J1.1, Q2.3 (E), R1.1, R2.1, R4.1, R10.1, R12.1, R14.1, R15.1
unnamed: D4.1 (K), R9.2
unnamed: Q1.2 (B), Q3.3 (E), R2.2, R11.1
unnamed: Q1.1 (C), R1.2
unnamed: Q2.2 (B), R4.2, R5.1
unnamed: Q2.1 (C), R3.1
unnamed: Q3.2 (B), R7.2
unnamed: Q3.1 (C), Q4.3 (E)
unnamed: Q4.2 (B), R8.2
unnamed: Q5.2 (B), R6.1
unnamed: Q5.3 (E), R5.2, R9.1
unnamed: Q6.2 (B), R11.2
unnamed: Q6.1 (C), R12.2, R13.1

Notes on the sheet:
(UNUSED)
SET0T
Manuelles Schalten
"GRÜN"
RCC_RGY_TVn_LED_V2 2026-08-23
CONTROL
"ROT"
RST0T



Board: 2 copper layers, 41.0 x 41.0 mm, 34 parts (2 on the bottom side), 22 nets.

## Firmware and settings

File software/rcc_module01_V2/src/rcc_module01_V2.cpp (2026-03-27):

//_____rcc_module01_V2___________________________khartinger_____
// This program for an ESP32 is used to test various self-built 
// model railroad switching blocks. The blocks are controlled 
// via the I/O pins of two I²C PCF8574 I/O expanders, whereby 
// the PCF8574 with the I2C address 0x20 (IO expander #0) is 
// used for control and the PCF8574 with the I2C address 0x21 
// (IO expander #1) for feedback. The IO pins for control and 
// feedback each have the same pin number.
//
// 1. DCC 11, IO expander pin 0: Decoupler (uncoupler)
// 2. DCC 21, IO expander pin 1,2: Two-way switch 
//    (with limit switch)
// 3. DCC 31,32, IO expander pin 3,4,5: Three-way switch
//    (with limit switching)
// 4. DCC 41, IO expander pin 6: Disconnectable track
// 5. DCC 51, IO expander pin 7: Flashing light
//
// The switching status of the components is shown 
// on a 1.54” OLED display.
//
// A button on pin D6 (IO19) can be used to skip the individual
// pages of the information display or to search for the WLAN.
//
// If you press the button for one second during the program 
// run, a reset is triggered. This can be used, for example, 
// to activate the WLAN when starting up again.
//
// All project-specific data, such as WLAN access, MQTT commands
// and hardware properties, are saved in a configuration file
// `dcc_config.h`.
//
// Required hardware
// Electronic components
// 1. ESP32 D1 mini
// 2. 1x do-it-yourself board “Shield_I2C_5V_3V3”: 
//    Connection for the two I2C buses
// 3. 1x DIY board “Shield_5V_DCC_6pol”: Power supply with 5V,
//    DCC signal and connection for button on pin D6 (IO19)
// 4. 1x OLED display with SSD1309 controller (e.g. 1.54“ or
//    2.4” displays with 128x64 pixel resolution)
// 5. 2x I²C expander boards PCF8574 with the (7-bit) 
//    addresses 0x20 and 0x21
// 6. push-button on pin D6 (IO19) with pull-up resistor 
//    (e.g. 10 kOhm) to 3.3V (or a wire)   
//
// Electrical components
// The electrical components depend on what you want to test.
// Example three-way crossover:
// 1. a three-way crossover with limit switching   
// 2. self-assembly block “RW_5V_W3” consisting of the two 
//    circuit boards `RW_5V_W3_STRG` and `RW_5V_W3_LED`
//    for controlling the points with 5V   
// 3. a transformer with 16V alternating voltage (V+, V-)
// 4. a DCC source for sending turnout commands (e.g. Roco 
//    MultiMAUS with digital amplifier 10764 and 
//    power supply 10850)
// 5. a 5V power supply   
//
// Class SimpleMqtt extends class PubSubClient for easy use.
// All commands of the PubSubClient class can still be used.
// Note: When PubSubClient lib is installed,
//       delete PubSubClient files in directory src/simplemqtt
// Important: Example needs a MQTT-broker!
// Created by Karl Hartinger, November 02, 2024
// Changes:
// 2025-03-12 Version 2025-01-18: Customization for module 12
// 2025-06-18 Add "signal", DEBUG_99_SHOW_ALL
// 2026-01-08 Update ../get bydcc, byname, one value
//            Add send MQTT-message if a value has changed
//            Add ../get status, RC_TYPE_TX, RC_TYPE_DCC
// 2026-01-11 Add ../set/wlan: get wlan data from eeprom
// 2026-02-24 Add ../get mac, setWiFiHostName()
// Released into the public domain.

// #include <Arduino.h>
// #include "src/pcf8574/D1_class_PCF8574.h"
//#define D1MINI          1              // ESP8266 D1mini +pro
#define  ESP32D1        2                   // ESP32 D1mini
#define  DEBUG_99       false               // true OR false
#define  DEBUG_99_SHOW_ALL  false           // true OR false
#define  LANGUAGE      'd'                  // 'd' or 'e'
#include "rcc_module01_V2_text.h"           // AFTER LANGUAGE
#include "pre_config.h"                     // common defines
#include "dcc_config.h"                     // hardware defines
#include <DccAccessoryDecoder.h>
#include "src/statemachine/D1_class_Statemachine.h"
#include "src/simplemqtt/D1_class_SimpleMqtt.h"
#include "src/screen154/D1_class_Screen154.h"

//_______declare method(s), if necessary________________________
String setRcompCmd(int iRcomp, int iCmdValue, String sReturn);
String actOnCmdHardware(int iCmd_, int iOutPCF_, 
                        int outBitA_, int outBitB_, int more_);
void showLine(int line_, String text_);
void showLine6WaitMaxXXs(int iSec, String line6);

//_______Global values and hardware_____________________________
#define  PIN_DCC        18                  // 18=D5
#define  PIN_BUTTON     19                  // 19=D6

//_______Global values for connection state_____________________
bool     bUseWiFi=false;
int      iConn=CON_UNKNOWN;                // WiFi unknown
int      iConnOld=CON_UNKNOWN;             // WiFi unknown

//_______Global values for updating the screen__________________
#define  NO_GROUP       -1                  // no group to show
//       buffer for lines for screen update
String   aScreenText[SCREEN_LINE_MAX];
//       sign per line: 1=normal display, -1=inverted
int      aScreenSign[SCREEN_LINE_MAX]={1,1,1,-1,1,1};
Screen154 screen_;
//-------Are info lines defined?--------------------------------
#ifdef INFOLINES
 String   infolines[INFOLINES_NUM] = INFOLINES;
#else
 #define INFOLINES_NUM  0
 String   infolines[] = {};
#endif

//_______Railroad commands______________________________________
//.......PCF8574 lines B A to control 2way turnout (active low!)
#define  CMD_NONE       -1   // no command
#define  CMD_BITA_ON    1    // set bit A=0 (inverted)
#define  CMD_BITA_OFF   2    // set bit A=1 (inverted)
#define  CMD_BIT2_ON    3    // bits BA = 00
#define  CMD_BIT2_A     4    // bits BA = 10
#define  CMD_BIT2_B     5    // bits BA = 01
#define  CMD_BIT2_OFF   6    // bits BA = 11
#define  CMD_BLINK      7    // start blink light
#define  CMD_BLINK_END  8    // stopp blink light

//.......All properties of a railroad command...................
// command: 0=out, 1=stright, 2=curved, 3=undefined (switching)
struct strRcmd {
  int     iCmd;         // command - what to do (now)
  int     inValue;      // current input value
  bool    inValueChanged; // true=yes, value has changed
  int32_t stateToDo;    // in which state should command be executed?
  int32_t stateOffset;  // additional state offset value
  int     iCmdOffset;   // command - what to do @ offset state
};
//.......Default values for all railroad commands...............
#define RCMD_NONE       CMD_NONE,-1,STATE_NONE,STATE_NONE,CMD_NONE
//.......Array of all current railway commands..................
// As there should only be one active command for one 
// component, aRcomp[] and aRcmd[] have the same size and the 
// same index for a command.
strRcmd aRcmd[RCOMP_NUM];

//_______State machine__________________________________________
#define STATE_MAX           180000     // 180000*20ms = 1 hour
#define STATE_DELAY             20     // state delay in ms
#define STATES_SCREEN_REFRESH  251     // 251*20ms=5,2s
#define STATES_SHOW_SCREEN_MIN  75     // show screen min 1.5 sec
#define STATES_BLINK            25     // 25*20ms =0,5s
#define STATES_BEFORE_RESET     50     // 25*20ms =1s
Statemachine stm(STATE_MAX, STATE_DELAY); //1..180000

//_______dcc access_____________________________________________
unsigned int dccAddress=0;             // dcc address
int dccValue=-1;                       // dcc input value

// *************************************************************
// DCC Callback Function
// *************************************************************

//_______DCC request____________________________________________
// Generate a command if the DCC address received belongs to a 
// component of the RW module.
// uses : aRcomp[]
// calls: setRcompCmd()
void onAccessoryPacket(unsigned int linearDecoderAddress, bool enabled) {
 digitalWrite(BUILTIN_LED, enabled ? 1 : 0);
 dccAddress=(int)linearDecoderAddress + DCC_OFFSET;
 dccValue=enabled ? 1 : 0;
 //------is it a DCC address for this module?-------------------
 for(int i=0; i<RCOMP_NUM; i++) {
  if(aRcomp[i].dcc==dccAddress) {
   //----railroad component found-------------------------------
   setRcompCmd(i, dccValue, "");
  }
 }
 if(DEBUG_99) {
  Serial.print("***Change in Accessory: ");
  Serial.print(dccAddress);
  Serial.print(" -> ");
  Serial.print(dccValue);
  Serial.println("***");
 }
}

#if _USE_WIFI_ == true
// *************************************************************
// Control functions for WLAN data
// *************************************************************
//_______Check IP-Address_______________________________________
// return: true = valid IP address, false: not valid
bool isValidIPv4(const String &ip) {
  int parts = 0;
  int last = 0;
  for (int i = 0; i <= ip.length(); i++) {
    if (i == ip.length() || ip[i] == '.') {
      if (i == last) return false;  // leerer Block
      int num = 0;
      for (int j = last; j < i; j++) {
        if (!isDigit(ip[j])) return false;
        num = num * 10 + (ip[j] - '0');
        if (num > 255) return false;
      }
      parts++;
      last = i + 1;
    }
  }
  return parts == 4;
}

//_______check WLAN input string________________________________
// input: ssid|password|ip
// if password ist empty: ssid||ip
bool validateWlanString(const String &s) {
  int i1 = s.indexOf('|');
  if (i1 < 0) return false;
  int i2 = s.indexOf('|', i1 + 1);
  if (i2 < 0) return false;
  // kein drittes '|'
  if (s.indexOf('|', i2 + 1) >= 0) return false;
  // ssid & password dürfen nicht leer sein
  if (i1 == 0) return false;                // ssid leer
  // if (i2 == i1 + 1) return false;        // password leer
  if (i2 == s.length() - 1) return false;   // ip leer
  // ip prüfen
  String ip = s.substring(i2 + 1);
  if (!isValidIPv4(ip)) return false;
  return true;
}
#endif

// *************************************************************
// MQTT Functions
// *************************************************************

#if _USE_WIFI_ == true
 //_______MQTT communication_____________________________________
 //SimpleMqtt client("..ssid..", "..password..","mqttservername");
 //SimpleMqtt client("Raspi11", "12345678","10.1.1.1", TOPIC_BASE);
 SimpleMqtt client(String(_SSID_), String(_PASS_),
                   String(_HOST_), String(TOPIC_BASE));

//_______MQTT: inspect all subscribed incoming messages_________
void callback(char* topic, byte* payload, unsigned int length)
{
 client.callback_(topic, payload, length);  // must be called!
}

//_______Answer get requests____________________________________
// sPayload: payload to message from TOPIC_GET
// auto answer: for help (+), version, ip (can be overwritten)
// return: ret answer payload for get request
String simpleGet(String sPayload)
{
 String p1=String("");                      // help string
 sPayload.toLowerCase();                    // for easy compare
 //-------------------------------------------------------------
  if(sPayload=="help" || sPayload=="?") {
  p1 ="+MQTT: ../set/w1 -m 1|g|G OR -m 0|A|a|B|b (set by name)\r\n";
  p1+="      ../set/11 -m 1|g|G OR -m 0|A|a|B|b (set by dcc address)\r\n";
  p1+="      ../get -m byname|bydcc (values of all components)\r\n";
  return p1;
 }
 //-------------------------------------------------------------
  if(sPayload=="version") {
  p1="{\"version\":\""; p1+= String(VERSION_99); p1+="\"}";
  return p1;
 }
 //-------------------------------------------------------------
 if(sPayload=="mac") {
  p1="{\"mac\":\""; p1+= client.getsMac();
  p1+="\",\"hostname\":\"" + client.getWiFiHostName();
  p1+="\"}";
  return p1;
 }
 //-------------------------------------------------------------
 if(sPayload=="ip") {
  p1="{\"ip\":\""; p1+= client.getsLocalIP(); p1+="\"}";
  return p1;
 }
 //-------------------------------------------------------------
 if(sPayload=="signal") {
  p1="{\"signal\":"; p1+=client.getsSignal(); p1+="}";
  return p1;
 }
 //-------------------------------------------------------------
 if(sPayload=="topicbase") {
  p1="{\"topicbase\":\""; p1+=client.getsTopicBase(); p1+="\"}";
  return p1;
 }
 //-------------------------------------------------------------
 if(sPayload=="eeprom") {
  int iResult1, iResult2;
  String s1=client.eepromReadTopicBase(iResult1);
  String s2=client.eepromReadMyData(iResult2);
  p1="{\"topicbase\":\"";
  if(iResult1>=0) p1+=s1;
  else
  {
   if(iResult1==-2) p1+="(no topic base)";
   else p1+=String("Error_#")+String(iResult1);
  }
  p1+="\",\"mydata\":\"";
  if(s2=="") p1+="(no data)";
  else p1+=s2;
  p1+="\"}";
  return p1;
 }
 
 //-------------------------------------------------------------
 String sUndef0=T_UNDEF0;
 String sUndef1=T_UNDEF1;
 String sStright=T_STRIGHT;
 String sCurved=T_CURVED;
 String sUnknown=T_UNKNOWN;
 String sON=T_ON;
 String sOFF=T_OFF;
 //-------------------------------------------------------------
 //------is it a get command for all railway components?--------
 if(sPayload=="byname" || sPayload=="bydcc" || sPayload=="status") {
  if(sPayload=="status")
  {
   sUndef0=T1_UNDEF0;
   sUndef1=T1_UNDEF1;
   sStright=T1_STRIGHT;
   sCurved=T1_CURVED;
   sUnknown=T1_UNKNOWN;
   sON=T1_ON;
   sOFF=T1_OFF;
  }
  p1="{";
  for(int i=0; i<RCOMP_NUM; i++) { // ...for all components.....
   if(i>0) p1+=",";
   if(sPayload=="byname") p1+="\"" + aRcomp[i].name + "\":\"";
   else p1+="\"" + String(aRcomp[i].dcc) + "\":\"";
   if(aRcomp[i].type==RC_TYPE_T3) {
    switch(aRcmd[i].inValue) {
     case 0:  p1+=sStright; break; // BA=00
     case 1:  p1+=sCurved;  break; // BA=01
     case 2:  p1+=sStright; break; // BA=10
     case 3:  p1+=sUndef1;  break; // BA=11
     default: p1+=sUnknown; break; // ?? impossible
    }
   }
   if(aRcomp[i].type==RC_TYPE_TO || aRcomp[i].type==RC_TYPE_TX) {
    switch(aRcmd[i].inValue) {
     case 0:  p1+=sUndef0;  break; // BA=00
      case 1:  p1+=sStright; break; // BA=01
      case 2:  p1+=sCurved;  break; // BA=10
      case 3:  p1+=sUndef1;  break; // BA=11
      default: p1+=sUnknown; break; // ?? impossible
    }
   }
   if(aRcomp[i].type==RC_TYPE_DT) { // discon track (fahrstrom)
    aRcmd[i].inValue ? p1+=sON : p1+=sOFF;
   }
   if(aRcomp[i].type==RC_TYPE_DD) { // double pole, double throw (2x UM)
    aRcmd[i].inValue ? p1+=T1_DPDT_1_NO : p1+=T1_DPDT_0_NC;
   }
   if(aRcomp[i].type==RC_TYPE_UC) {
    aRcmd[i].inValue ? p1+=sON : p1+=sOFF;
   }
   if(aRcomp[i].type==RC_TYPE_BL) {
    // aRcmd[i].inValue ? p1+=sON : p1+=sOFF;
    if(aRcmd[i].iCmd==CMD_BLINK) p1+=sON; else p1+=sOFF;
   }
   p1+="\"";
  } // END OF for all components................................
  p1+="}";
  return p1;
 }

//-------------------------------------------------------------
 //------is it a get command for ONE railway component by dcc or name?
 for(int i=0; i<RCOMP_NUM; i++) { // ...for all components.....
  String s1=String(aRcomp[i].name);
  s1.toLowerCase();
  String s2=String(aRcomp[i].dcc);
  p1="";
  if(sPayload==s1) p1="{\""+s1+"\":\""; // by name
  if(sPayload==s2) { // by dcc
   p1="{\""+s2+"\":\"";
   sUndef0=T1_UNDEF0;
   sUndef1=T1_UNDEF1;
   sStright=T1_STRIGHT;
   sCurved=T1_CURVED;
   sUnknown=T1_UNKNOWN;
   sON=T1_ON;
   sOFF=T1_OFF;
  }
  if(p1.length()>0) {
   if(aRcomp[i].type==RC_TYPE_T3) {
    switch(aRcmd[i].inValue) {
     case 0:  p1+=sStright; break; // BA=00
     case 1:  p1+=sCurved;  break; // BA=01
     case 2:  p1+=sStright; break; // BA=10
     case 3:  p1+=sUndef1;  break; // BA=11
     default: p1+=sUnknown; break; // ?? impossible
    }
   }
   if(aRcomp[i].type==RC_TYPE_TO || aRcomp[i].type==RC_TYPE_TX) {
    switch(aRcmd[i].inValue) {
     case 0:  p1+=sUndef0;  break; // BA=00
      case 1:  p1+=sStright; break; // BA=01
      case 2:  p1+=sCurved;  break; // BA=10
      case 3:  p1+=sUndef1;  break; // BA=11
      default: p1+=sUnknown; break; // ?? impossible
    }
   }
   if(aRcomp[i].type==RC_TYPE_DT) { // discon track (fahrstrom)
    aRcmd[i].inValue ? p1+=sON : p1+=sOFF;
   }
   if(aRcomp[i].type==RC_TYPE_DD) { // double pole, double throw (2x UM)
    aRcmd[i].inValue ? p1+=T1_DPDT_1_NO : p1+=T1_DPDT_0_NC;
   }
   if(aRcomp[i].type==RC_TYPE_UC) {
    aRcmd[i].inValue ? p1+=sON : p1+=sOFF;
   }
   if(aRcomp[i].type==RC_TYPE_BL) {
    if(aRcmd[i].iCmd==CMD_BLINK) p1+=sON; else p1+=sOFF;
    //aRcmd[i].inValue ? p1+=sON : p1+=sOFF;
   }
   p1+="\"}";
   return p1;
  }
 } // END OF for all components.................................
 //-------------------------------------------------------------
 return String("");                         // wrong Get command
}
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
void loop() {
 //======(1) do at the beginning of the loop ...================
 int state=stm.loopBegin();                 // state begin
 String s1;                                 // help value
 String sSerial=String(state);              // collect serial output
 int retDCC_=-1;                            // if value changed

 //======(2) do, independent on the network, ...================
 
 //------(2.1) button handling (reset by software)--------------
 if(digitalRead(PIN_BUTTON)==0) {
  //.....button pressed (0).....................................
  if(reset_countdown<0) reset_countdown=STATES_BEFORE_RESET;
  else reset_countdown--;
  sSerial+="Resetcounter="+String(reset_countdown);
  //.....time for reset?........................................
  if(reset_countdown==0) { // yes, time for reset
   screen_.clear();
   screen_.useFontTitle();
   screen_.drawString(50,30,String("RESET"));
   esp_restart();
  } // END OF yes, time for reset
 } else {
  //.....button not pressed (1).................................
  reset_countdown=-1;
 }

 //------(2.2) For all comp: replace STATE_NOW by current state-
 for(int i=0; i<RCOMP_NUM; i++) { // for all components
  if(aRcmd[i].stateToDo==STATE_NOW) {
   aRcmd[i].stateToDo=state;
   if(aRcmd[i].stateOffset!=STATE_NONE) {
    aRcmd[i].stateOffset=stm.add(aRcmd[i].stateOffset);
   }
  }
 } // END OF for all components

 //------(2.3) update all input values into aRcomp[]------------
 int iRcomp_=updateInputValues();            // get input

 //------(2.4) update display, if there was an input change-----
 if(iRcomp_>=0) { // yes, input changed
  //.....prepare display........................................
  int iRcompGroup_=int(iRcomp_/5);
  if(iRcompGroup_== iRcompGroupNow)
  { // change in current displayed group: show change-----------
   prepareScreenLine4to6(iRcompGroupNow);
   showScreenLine4to6();
  } else { // another group should be shown.....
   iRcompGroupNext=iRcompGroup_;
  }
 } // END OF yes, input changed

 //------(2.5) refresh screen-----------------------------------
 if(state >= stateNextScreenMin)
 { // .......screen refresh allowed.............................
  if(iRcompGroupNext != NO_GROUP) {
   prepareScreenLine4to6(iRcompGroupNext);
   refreshScreen();
   stateNextScreenRefresh=stm.add(STATES_SCREEN_REFRESH);
   stateNextScreenMin=stm.add(STATES_SHOW_SCREEN_MIN);
   iRcompGroupNext = NO_GROUP;
   if(iRcompGroupNow>0) iRcompGroupNow--;
   else iRcompGroupNow=int((RCOMP_NUM-1)/5);

  }
 } // END OF screen refresh allowed
 if(state >= stateNextScreenRefresh)
 { // .......standard screen refresh............................
  iRcompGroupNow++;
  if(5*iRcompGroupNow > RCOMP_NUM) iRcompGroupNow=0;
  prepareScreenLine4to6(iRcompGroupNow);
  refreshScreen();
  iRcompGroupNext = NO_GROUP;
  stateNextScreenRefresh=stm.add(STATES_SCREEN_REFRESH);
  stateNextScreenMin=stm.add(STATES_SHOW_SCREEN_MIN);
 } // END OF standard screen refresh

 //======(3) process mqtt actions===============================
 #if _USE_WIFI_ == true
 if(bUseWiFi) {
  //.....Force an MQTT get message because a value has changed..
  //if(retDCC_>=0) {
  // client.publish_P((String(TOPIC_BASE)+"/get").c_str(),String(retDCC_).c_str(),false);
  //}
  //.....process mqtt actions...................................
  client.doLoop();                          // mqtt loop
  //=====(4) do, depending on the network access, ...===========
  if(client.isWiFiConnectedNew())    iConn=CON_WIFI_OK;// "WiFi OK   ";
  if(client.isMQTTConnectedNew())    iConn=CON_MQTT_OK;// "MQTT OK   ";
  if(client.isMQTTDisconnectedNew()) iConn=CON_NO_MQTT;// "-No MQTT--";
  if(client.isWiFiDisconnectedNew()) iConn=CON_NO_WIFI;// "-No WiFi--";
 } else {
  iConn=CON_WIFI_NOT_USED;                  // "unused WiFi"
 }
 //------show WLAN-/MQTT-connection status----------------------
 if(iConn!=iConnOld) {
  iConnOld=iConn;
  sSerial+=" | "+sConn[iConn];
  showLine(2,sConn[iConn]+" "+client.getsSSID());
 }
 #endif

 //======(4) do things after mqtt access========================
 //------act on a command---------------------------------------
 s1=actOnCmd(state);
 if(s1!="") sSerial+=" | "+s1;

 //======(5) do at the end of the loop ...======================
 DccAccessoryDecoder.loop();
 if(dccAddress>=0 && dccAddress<2048) {
  sSerial+=" | DCC Adresse="+String(dccAddress)+" Wert="+String(dccValue);
  dccAddress=-1;
 }
 uint32_t ms=stm.loopEnd();                   // state end
 //------print serial data--------------------------------------
 if(DEBUG_99) {
 sSerial+=" | ";
  sSerial+=String(ms);
  if(ms>STATE_DELAY) sSerial+=" ms-Too long!!";
  else sSerial+=" ms";
  if(DEBUG_99_SHOW_ALL) Serial.println(sSerial);
  else {
   if(sSerial.length()>14) Serial.println(sSerial);
  }
 }
}

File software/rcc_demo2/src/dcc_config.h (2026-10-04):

//_____dcc_config.h______________________________khartinger_____
// Configure file for ESP32 railroad DCC decoder program
// rcc_demo2
// Created by Karl Hartinger, November 14, 2024
// Changes:
// 2024-11-28 Change program name
// 2025-01-03 Change TOPIC_BASE
// 2025-06-18 Add "signal"
// 2026-01-08 Add RC_TYPE_TX, RC_TYPE_DD
// 2026-02-24 Add mac
// 2026-08-17 Add dcc_config.cpp, Redesign constexpr, ...
// 2026-09-13 Add RC_TYPE_TUI
// 2026-10-02 Add RC_TYPE_P1
// Released into the public domain.

#ifndef DCC_CONFIG_H
 #define DCC_CONFIG_H
 #include "pre_config.h"                    // common defines
 #include <Arduino.h>                       // String, int32_t
 #include "src/pcf8574/D1_class_PCF8574.h"  // PCF8574
 #include "src/statemachine/D1_class_Statemachine.h" // STATE_NONE

//_______show debug information_________________________________
#define  DEBUG_99       false               // true OR false
#define  DEBUG_99_SHOW_ALL  false           // true OR false

//_______program version________________________________________
constexpr char VERSION_99[] = "2026-10-02 rcc_demo2";
constexpr char VERSION_99_1[] = "Version 2026-10-02";

//_______Network data___________________________________________
#define _USE_WIFI_      true
constexpr char _SSID_[] = "Raspi11";
constexpr char _PASS_[] = "12345678";
constexpr char _HOST_[] = "10.1.1.1";
constexpr char _ESP_NAME_[] = "rccdemo2";

//_______MQTT data______________________________________________
constexpr char TOPIC_BASE[] = "rcc/demo2";
constexpr char TOPIC_GET[] = "?,help,version,mac,ip,signal,topicbase,eeprom,byname,bydcc,status";
constexpr char TOPIC_SET[] = "topicbase,wlan,eeprom0";
constexpr char TOPIC_SUB[] = "";
constexpr char TOPIC_PUB[] = "";

//_______1.54" display data (SSD1309, 128x64 pixel, I2C)________
constexpr char SCREEN_TITLE[] = "RCC_Demo2";
constexpr int  SCREEN_LINE_MAX = 6;
constexpr int  SCREEN_LINE_LEN = 21;
constexpr int  SHOW_INFOPAGE_SEC = 20; // time to show one page

//_______DCCex__________________________________________________
constexpr int  DCC_OFFSET = 4;

//_______Software: Railroad commands____________________________
//.......PCF8574 lines B A to control 2way turnout (active low!)
constexpr int CMD_NONE = -1;      // no command
constexpr int CMD_BIT_A_0 = 1;    // set bit A=0 (inverted)
constexpr int CMD_BIT_A_1 = 2;    // set bit A=1 (inverted)
constexpr int CMD_BIT_BA_00 = 3;  // bits BA = 00
constexpr int CMD_BIT_BA_10 = 4;  // bits BA = 10
constexpr int CMD_BIT_BA_01 = 5;  // bits BA = 01
constexpr int CMD_BIT_BA_11 = 6;  // bits BA = 11
constexpr int CMD_BLINK = 7;      // start blinking light
constexpr int CMD_BLINK_END =8;   // stop blinking light

//.......All properties of a railroad command...................
// command: 0=out, 1=straight, 2=curved, 3=undefined (switching)
struct strRcmd {
  int     iCmd;         // command - what to do (now)
  int     inValue;      // current input value
  bool    inValueChanged; // true=yes, value has changed
  int32_t stateToDo;    // in which state should command be executed?
  int32_t stateOffset;  // additional state offset value
  int     iCmdOffset;   // command - what to do @ offset state
};
//.......Default values for all railroad commands...............
#define RCMD_NONE       CMD_NONE,-1,STATE_NONE,STATE_NONE,CMD_NONE

//_______Hardware: IO expander PCF8574__________________________
// Assumption: IO boards on I2C bus #1, initial value 0xFF.
// Changes can be made in file dcc_config.cpp

// ***** CHECK this! *******************************************
#define  IOEX_NUM       4         // number of IO expander 2|4|6|8

//.......Suggested addresses....................................
#define  IOEX_ADDRESS1  0x20      // pcf8574_out #1
#define  IOEX_ADDRESS2  0x21      // pcf8574_in  #1
#define  IOEX_ADDRESS3  0x22      // pcf8574_out #2
#define  IOEX_ADDRESS4  0x23      // pcf8574_in  #2
#define  IOEX_ADDRESS5  0x24      // pcf8574_out #3
#define  IOEX_ADDRESS6  0x25      // pcf8574_in  #3
#define  IOEX_ADDRESS7  0x26      // pcf8574_out #4
#define  IOEX_ADDRESS8  0x27      // pcf8574_in  #4
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

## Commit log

2024-11-27 KiCad files of the RCC components
    [AC_5V_6pol_DCC_V1.kicad_pcb, AC_5V_6pol_DCC_V1.kicad_sch, Box_02x03_P2.54_Vertikal.step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]
2024-11-27 Update ESP32 README.md
2024-11-28 KiCad DCC Shield
    [Shield_5V_DCC_6pol_V3.kicad_pcb, Shield_5V_DCC_6pol_V3.kicad_sch]
2024-11-28 KiCad I2C Shield
    [Shield_I2C_5V_3V3_V2.kicad_pcb, Shield_I2C_5V_3V3_V2.kicad_sch]
2024-11-28 Add KiCad files
    [CON_10pol_PIN_V2.kicad_pcb, CON_10pol_PIN_V2.kicad_sch, CON_6pol_3_V1.kicad_pcb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]
2024-11-28 ESP32 demo software
2024-11-28 move KiCad files
    [RW_5V_1OUT_LED_V2.kicad_pcb, RW_5V_1OUT_LED_V2.kicad_sch, RW_5V_1OUT_STRG_V1.kicad_pcb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]
2025-02-09 Add 3D files
    [Bracket_sub-D_250209.3mf, ModulSeite_250209.3mf, OLED-Mount_250209.3mf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]
2025-02-12 Update 3d data
    [Bracket_sub-D_250209.3mf, ModulSeite_250209.3mf, OLED-Mount_250209.3mf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]
2025-02-12 move /kicad to fab/kicad
    [AC_5V_6pol_DCC_V1.kicad_pcb, AC_5V_6pol_DCC_V1.kicad_sch, Box_02x03_P2.54_Vertikal.step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]
2025-02-16 Update rcc3_i2c
    [CON_10pol_2x4_V1.kicad_pcb, CON_10pol_2x4_V1.kicad_sch, CON_1xIO_V2.kicad_pcb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]
2025-02-22 Update kicad-Files
    [CON_10pol_2x4_V1.kicad_sch, CON_1xIO_V2.kicad_sch, CON_6pol_6_V2.kicad_sch]
2025-03-04 Update kicad files
    [CON_1xIO_V1.kicad_pcb, CON_1xIO_V1.kicad_sch, CON_2xIO_V1.kicad_pcb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]
2025-03-05 Update RCC_5V_Parts
    [RCC_5V_Parts_350304.ods]
2025-03-06 Update kicad ..SUB25..
    [RW_5V_2SUB25_V4.kicad_pcb, RW_5V_2SUB25_V4.kicad_sch, RW_5V_SUB25_10_V3.kicad_pcb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]
2025-03-07 Update LED config
2025-03-09 Update Parts
    [RCC_5V_Parts_350309.ods]
2025-03-12 Module01 created
    [RCC_5V_Parts_350309.ods]
2025-03-28 Replace äöü
    [CON_SubD_Screw10_V1.kicad_sch, RW_5V_1OUT_LED_V2.kicad_pcb, RW_5V_1OUT_LED_V2.kicad_sch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]
2025-03-31 Add 3d: turnout cover
    [Weichenabdeckung_2Weg_1_v4.3mf, Weichenabdeckung_2Weg_1_v4.f3d, Weichenabdeckung_2Weg_flach v1.3mf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]
2025-04-16 Add some PCBs
2025-10-15 Add FreeCAD files
    [Bracket_sub-D.FCStd, ModulSeiteEingleisig.FCStd, OLED_Mount.FCStd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]
2025-11-21 Update dust_cover and freecad files
    [Bohrhilfe_klein_251114.FCStd, Klammer265.FCStd, ModulSeiteEingleisig_251109.FCStd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]
2025-11-21 Update Freecad Files and LIESMICH.md
    [Biegelehre_LED.FCStd, ModulStützeEingleisig_251109.FCStd, ModulStützeZweigleisig_251109.FCStd]
2026-01-10 Update rcc_module13 ESP32 software
2026-04-27 Add ModulStütze Version 260427
    [ModulStützeEingleisig_260427.FCStd, ModulStützeZweigleisig_260427.FCStd]
